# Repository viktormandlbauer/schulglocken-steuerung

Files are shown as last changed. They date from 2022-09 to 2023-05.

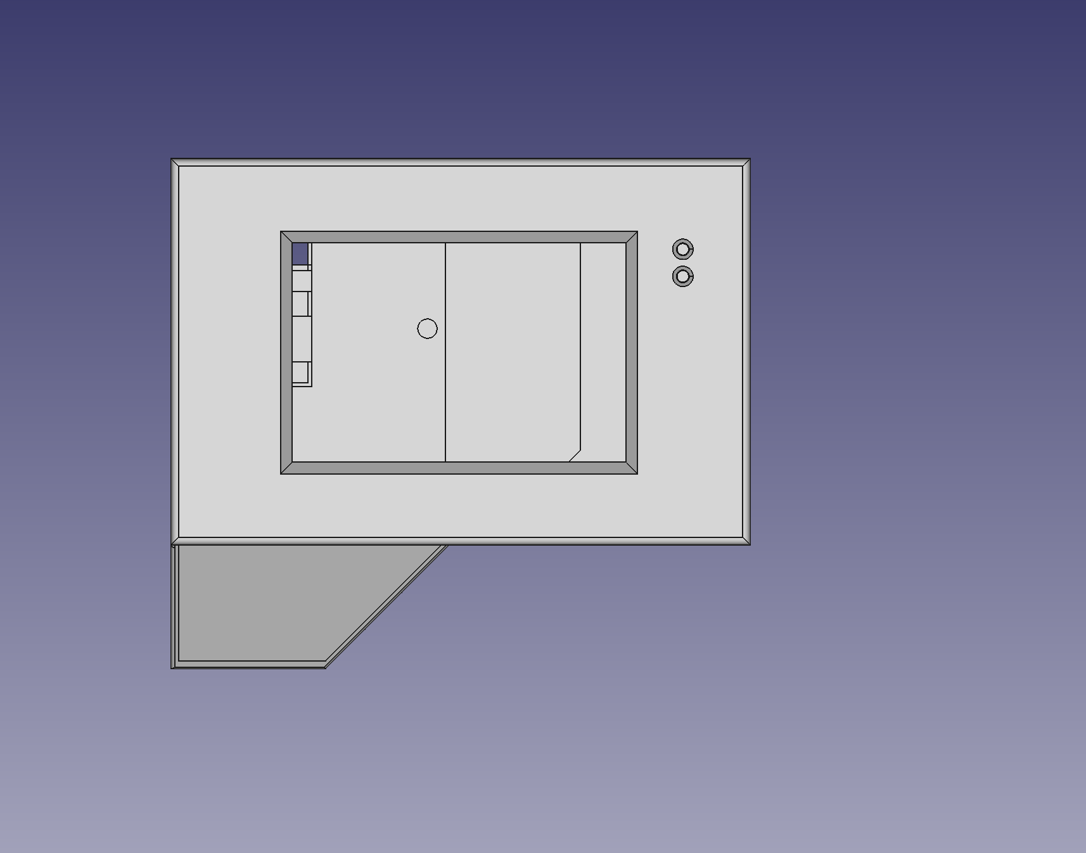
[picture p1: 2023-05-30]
cad/Freecad/CASE/A1_IMG/DiplPRJ3.png

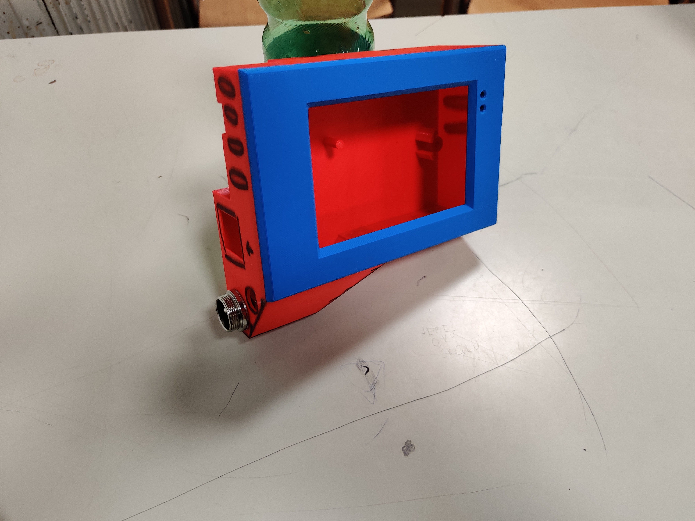
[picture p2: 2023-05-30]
cad/Freecad/CASE/A1_IMG/IMG_20230503_201758.jpg

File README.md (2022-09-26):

# schulglocken-steuerung
Google Drive Project:    
https://drive.google.com/drive/folders/1yu67mSQ9u2VfD9QC0o6wKGEjTrWiLxPo?usp=sharing

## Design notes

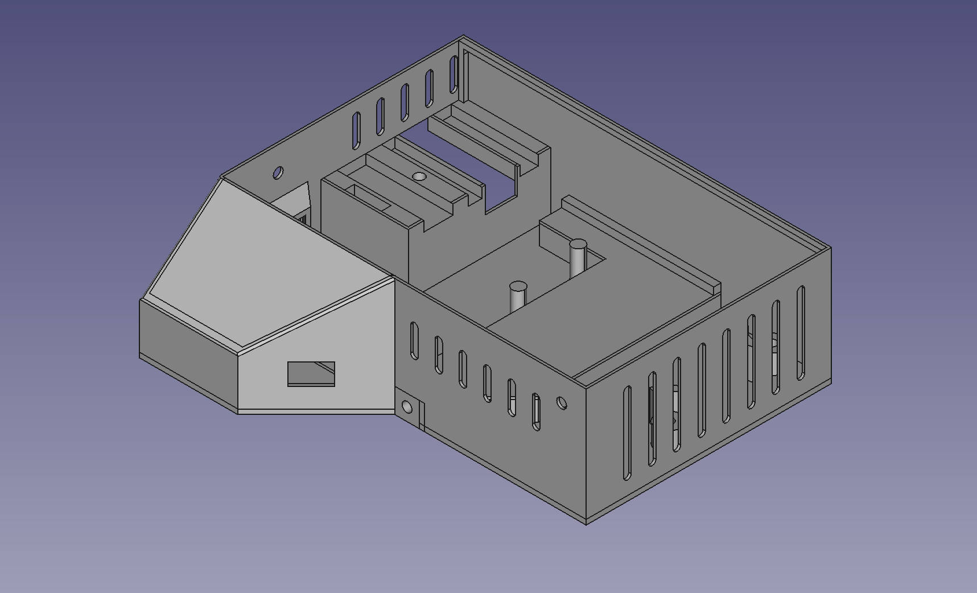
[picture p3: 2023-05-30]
cad/Freecad/CASE/A1_IMG/DiplPRJ4.png

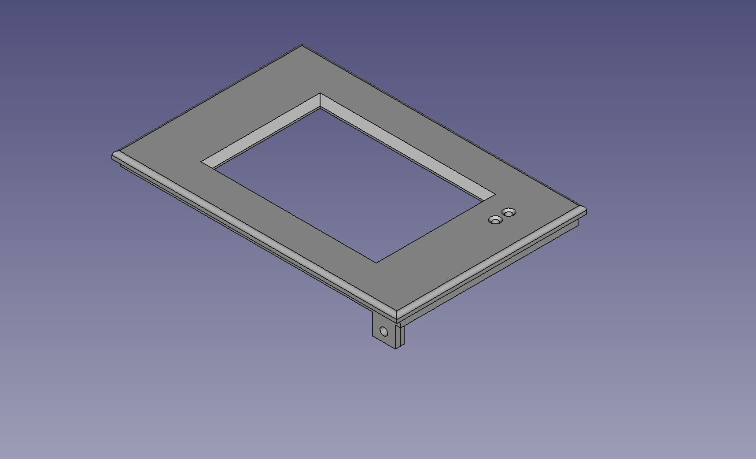
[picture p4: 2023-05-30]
cad/Freecad/CASE/A1_IMG/DiplPRJ5.png

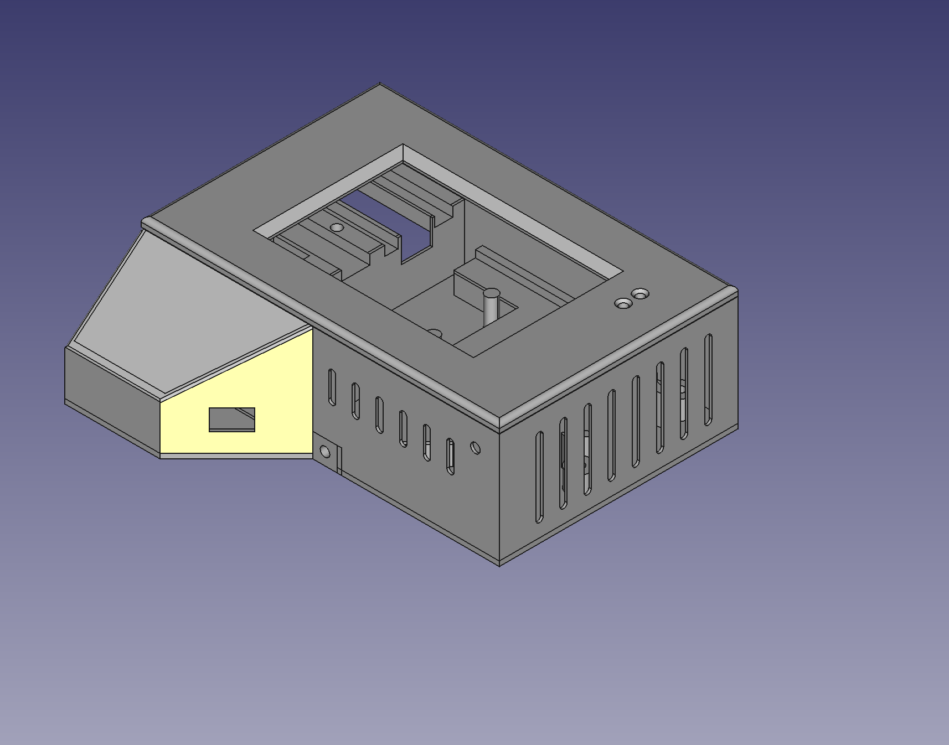
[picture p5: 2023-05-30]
cad/Freecad/CASE/A1_IMG/DiplPRJ2.png

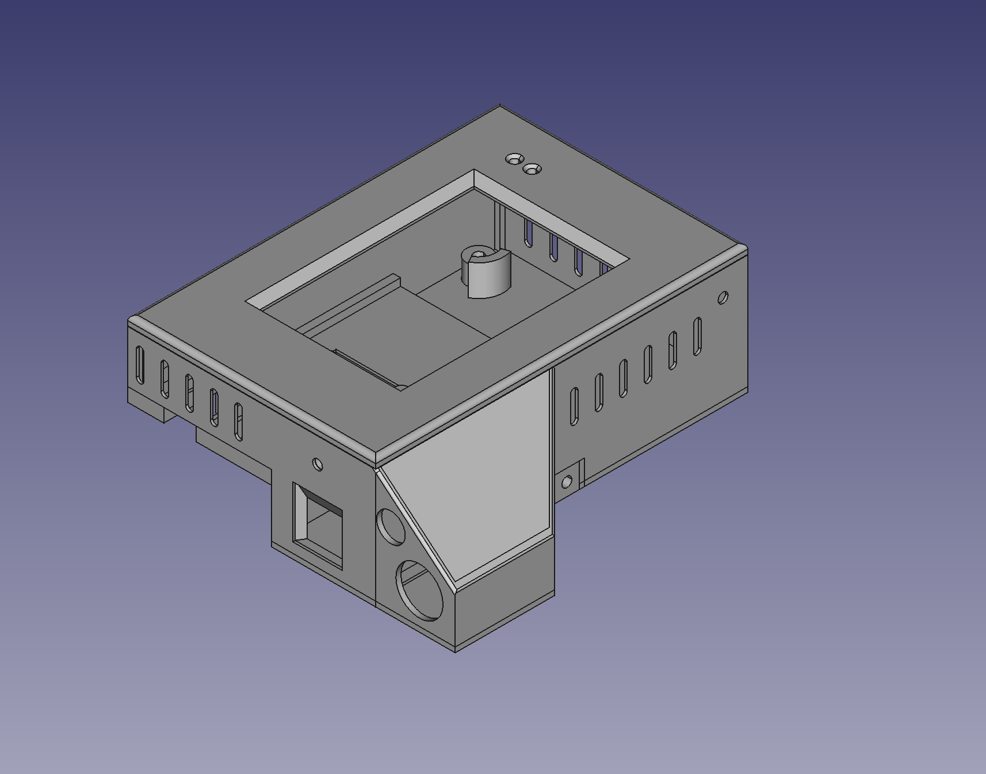
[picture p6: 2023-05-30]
cad/Freecad/CASE/A1_IMG/DiplPRJ1.png

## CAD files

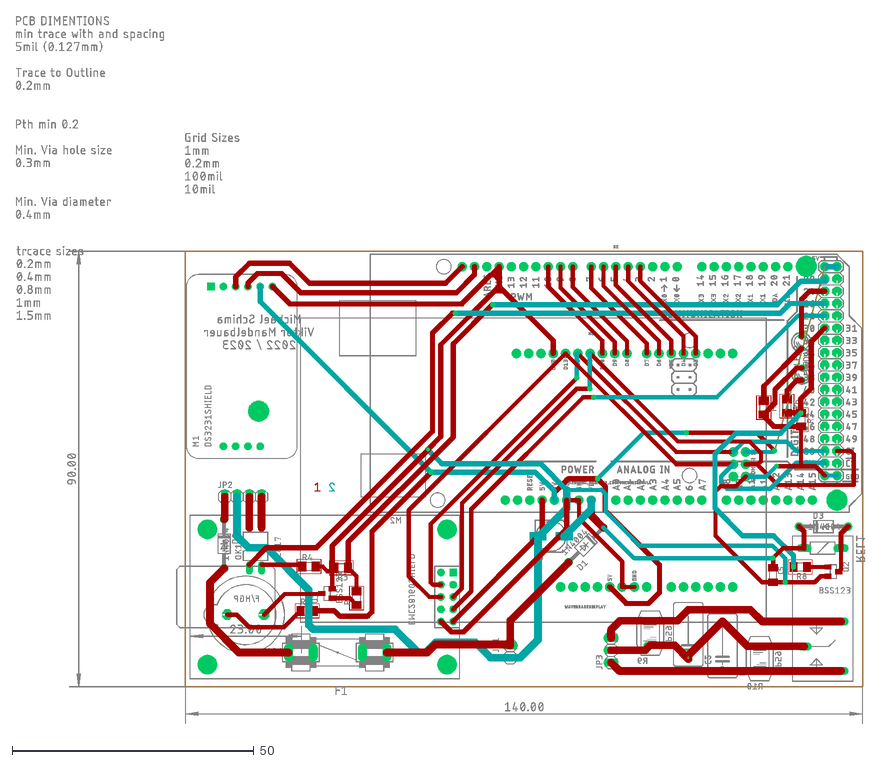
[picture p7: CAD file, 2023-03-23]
cad/Eagle/Eagle MainPCB/Schulglocke_PCB.dxf
175.5 x 146.2

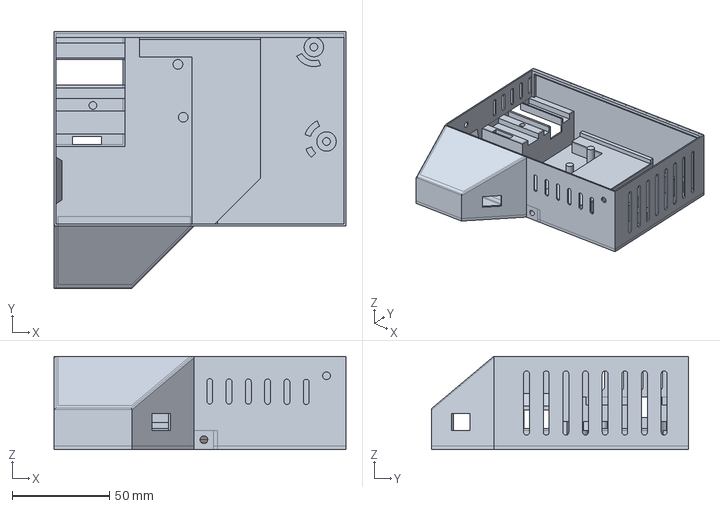
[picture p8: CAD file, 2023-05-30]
cad/Freecad/CASE/leftcorner_v5.FCStd
150.0 x 132.0 x 48.0 mm
base body witch cut out001
WallBracket

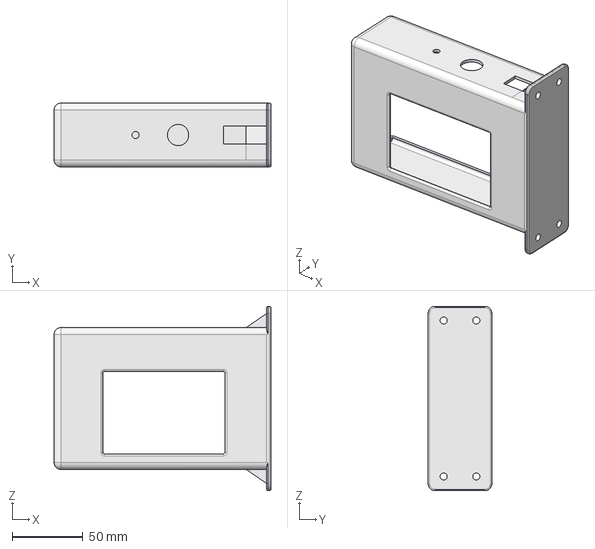
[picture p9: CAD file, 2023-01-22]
cad/Freecad/DEMO1/demo1_cut.FCStd
153.0 x 45.0 x 130.0 mm

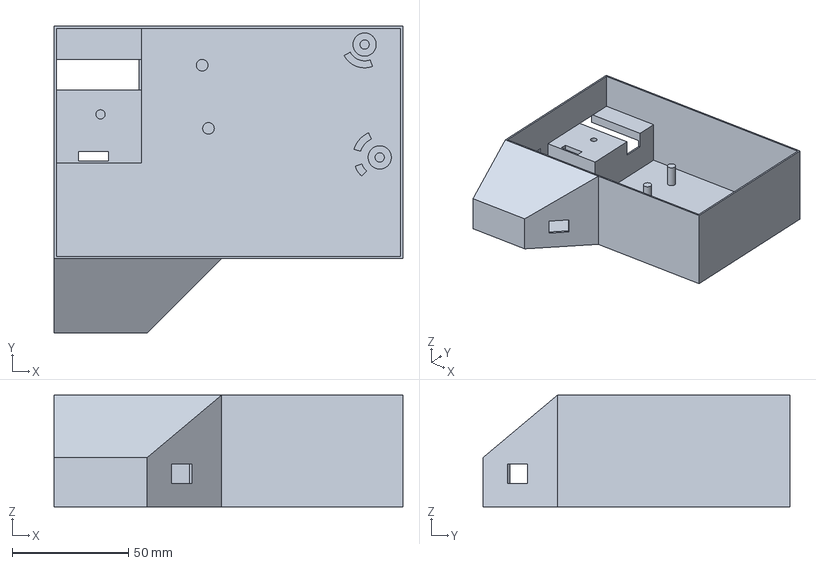
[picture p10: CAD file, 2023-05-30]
cad/Freecad/CASE/leftcorner-base body witch cut out001.3mf
150.0 x 132.0 x 48.0 mm

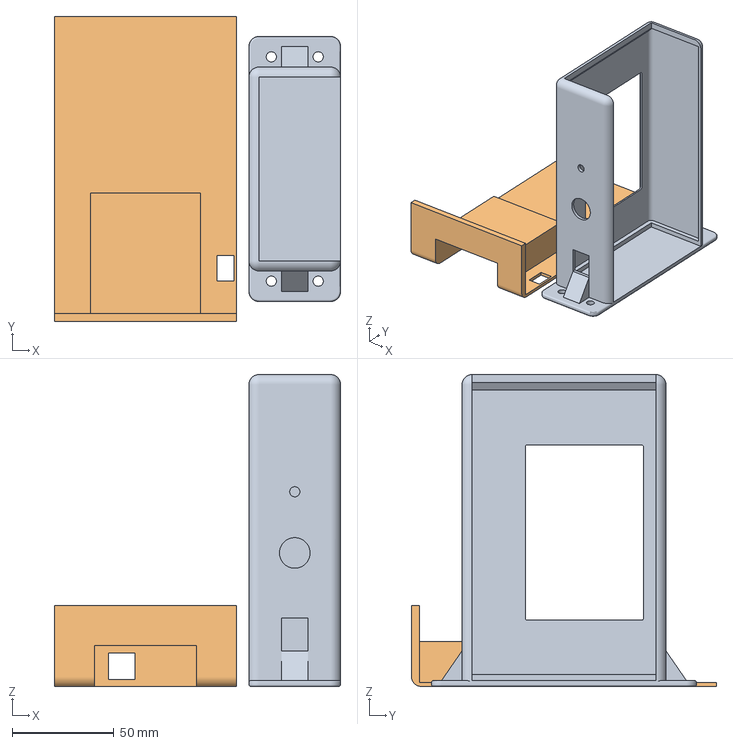
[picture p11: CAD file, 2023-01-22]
cad/Freecad/DEMO1/demo1_cut-Body006.3mf
140.4 x 149.7 x 153.0 mm
demo1_cut-Body006

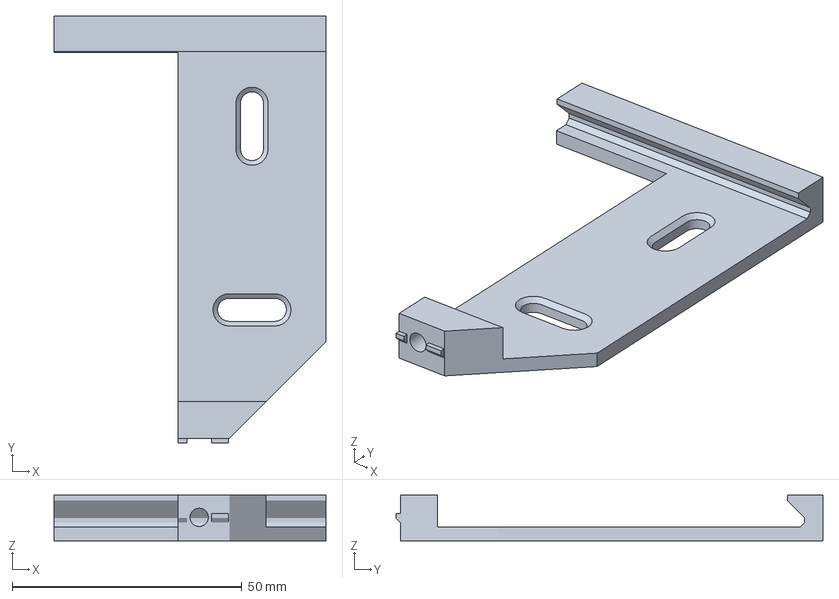
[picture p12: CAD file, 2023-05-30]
cad/Freecad/CASE/leftcorner_v5-WallBracket.3mf
59.2 x 93.0 x 10.0 mm

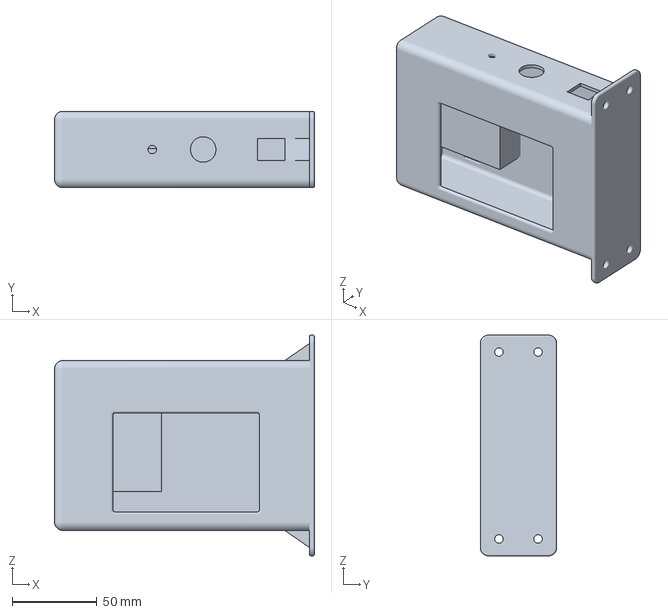
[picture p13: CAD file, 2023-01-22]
cad/Freecad/DEMO1/demo1-Body.3mf
153.0 x 45.0 x 130.0 mm

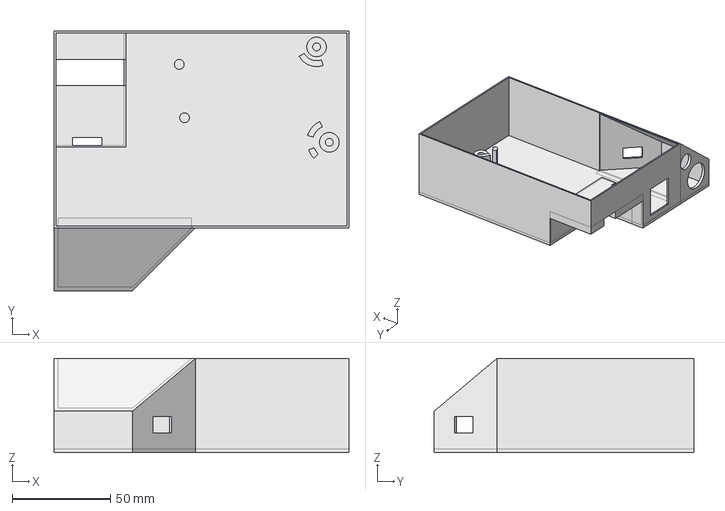
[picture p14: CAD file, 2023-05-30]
cad/Freecad/CASE/leftcorner.FCStd
150.0 x 132.0 x 48.0 mm

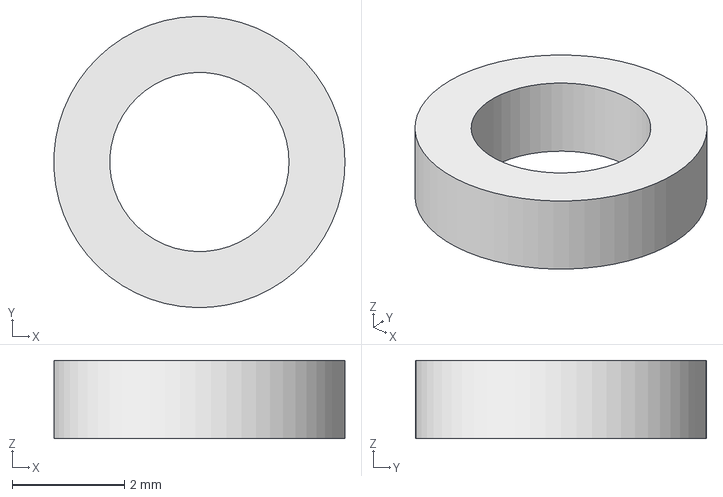
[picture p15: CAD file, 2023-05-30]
cad/Freecad/CASE/isolation.FCStd
5.20 x 5.20 x 1.40 mm

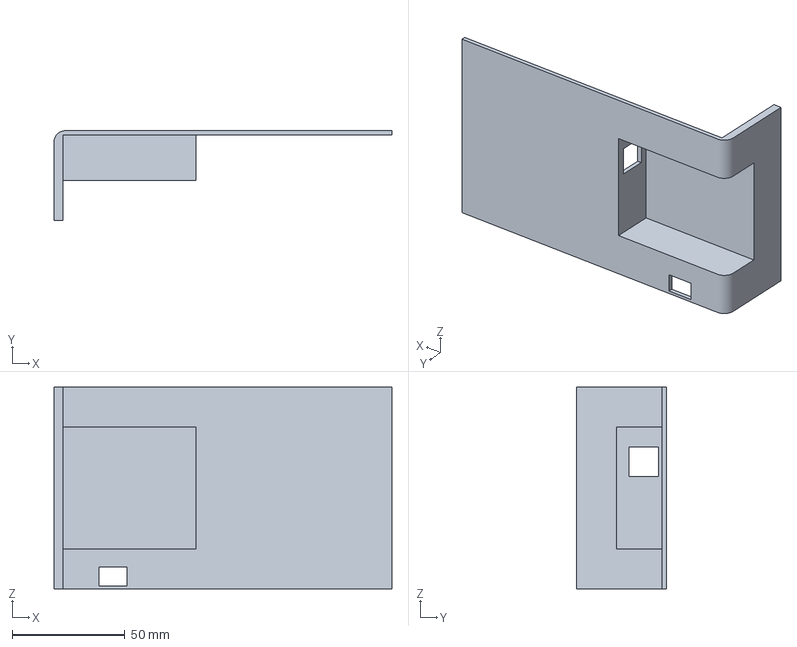
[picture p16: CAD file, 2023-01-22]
cad/Freecad/DEMO1/part2.3mf
149.7 x 39.7 x 89.4 mm

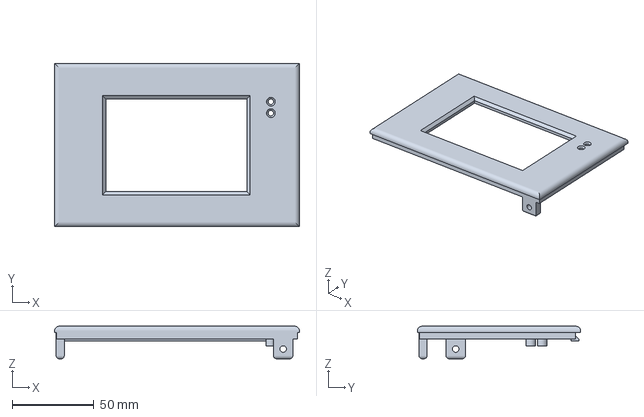
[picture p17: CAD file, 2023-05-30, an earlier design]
cad/Freecad/CASE/leftcorner_v4-Body008.3mf
150.0 x 100.0 x 20.0 mm

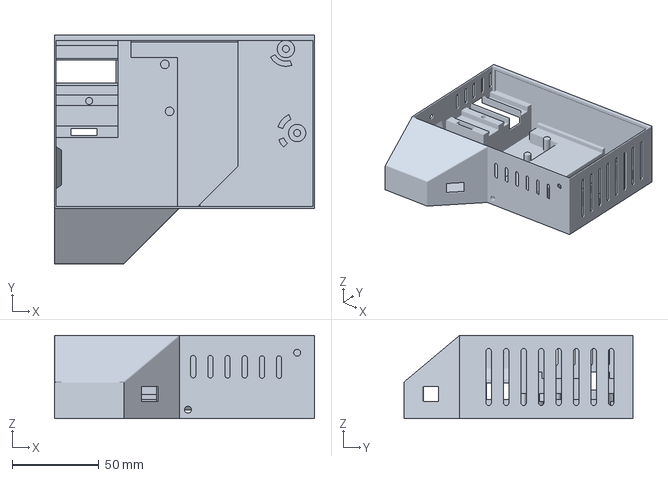
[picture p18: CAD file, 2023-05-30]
cad/Freecad/CASE/leftcorner_v4-base body witch cut out001.3mf
150.0 x 132.0 x 48.0 mm

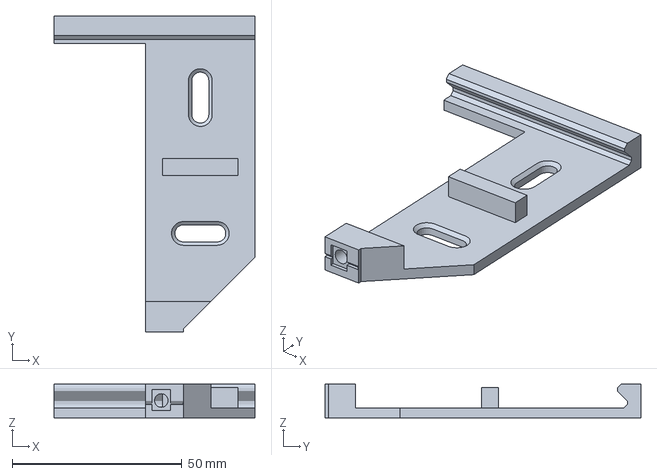
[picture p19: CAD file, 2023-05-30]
cad/Freecad/CASE/leftcorner_v5-WallBracketPad041.3mf
59.2 x 93.0 x 10.0 mm

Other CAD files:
cad/Freecad/DEMO1/demo1.FCStd
cad/Freecad/DEMO1/part1.3mf
cad/Freecad/CASE/leftcorner-MOUNT_v3-Body.3mf
cad/Freecad/CASE/isolation-Body.3mf
cad/Freecad/CASE/1.FCStd
cad/Freecad/CASE/1-Body007.3mf
cad/Freecad/CASE/1-base body witch cut out001.3mf
cad/Freecad/CASE/1_long edge.FCStd
cad/Freecad/CASE/leftcorner_v2.FCStd
cad/Freecad/CASE/leftcorner_v3-base body witch cut out001.3mf
cad/Freecad/CASE/leftcorner_v3.FCStd
cad/Freecad/CASE/leftcorner_v4.FCStd

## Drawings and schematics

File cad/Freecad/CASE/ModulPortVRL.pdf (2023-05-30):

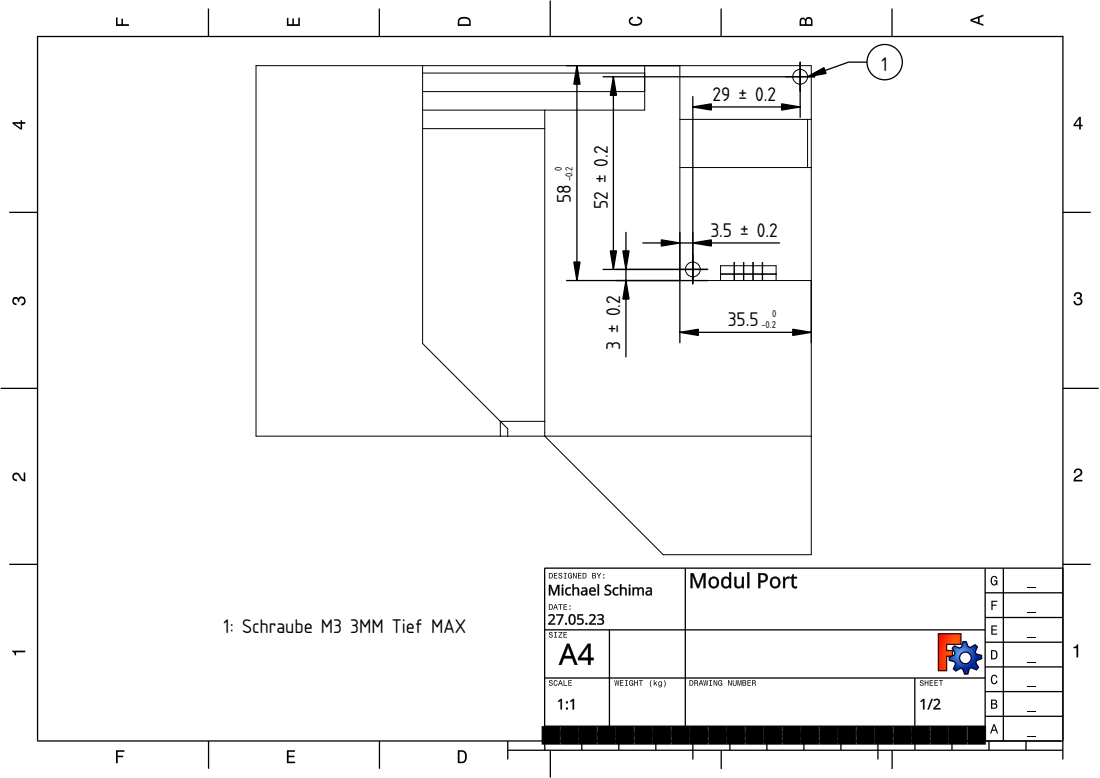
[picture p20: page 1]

1: Schraube M3 3MM Tief MAX

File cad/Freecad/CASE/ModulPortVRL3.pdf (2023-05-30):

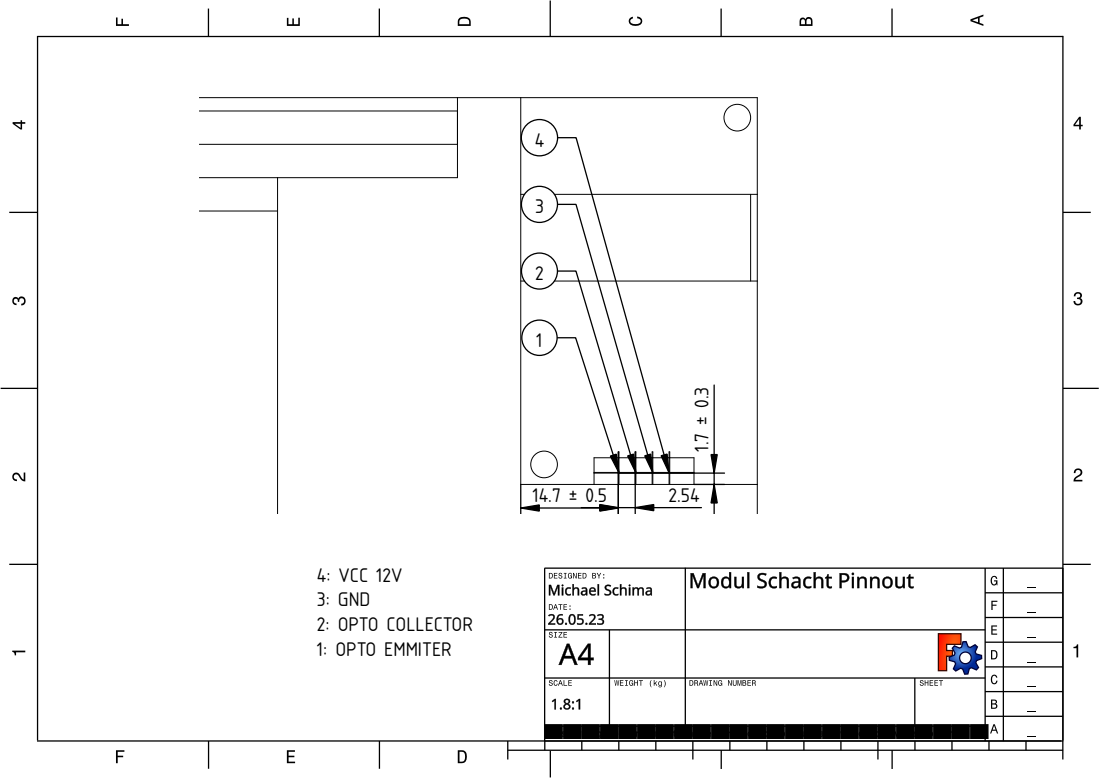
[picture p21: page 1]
4: VCC 12V 3: GND 2: OPTO COLLECTOR 1: OPTO EMMITER

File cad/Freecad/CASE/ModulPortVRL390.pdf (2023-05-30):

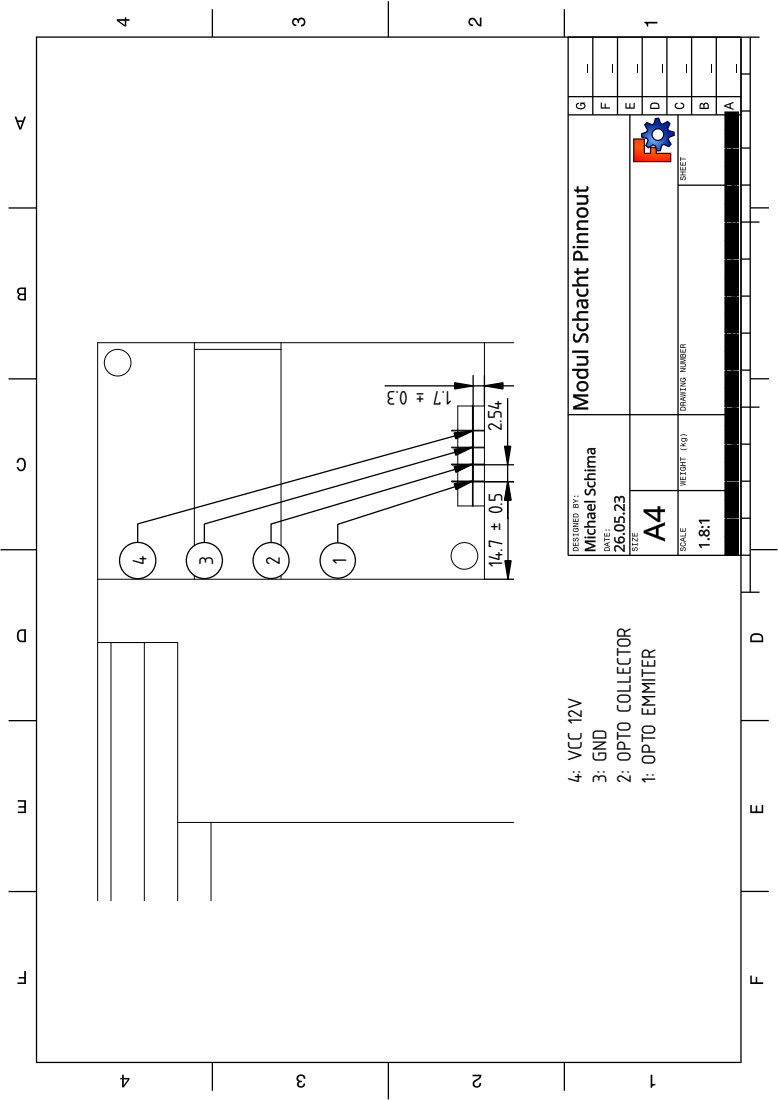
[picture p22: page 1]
4: VCC 12V; 3: GND; 2: OPTO COLLECTOR 1: OPTO EMMITER

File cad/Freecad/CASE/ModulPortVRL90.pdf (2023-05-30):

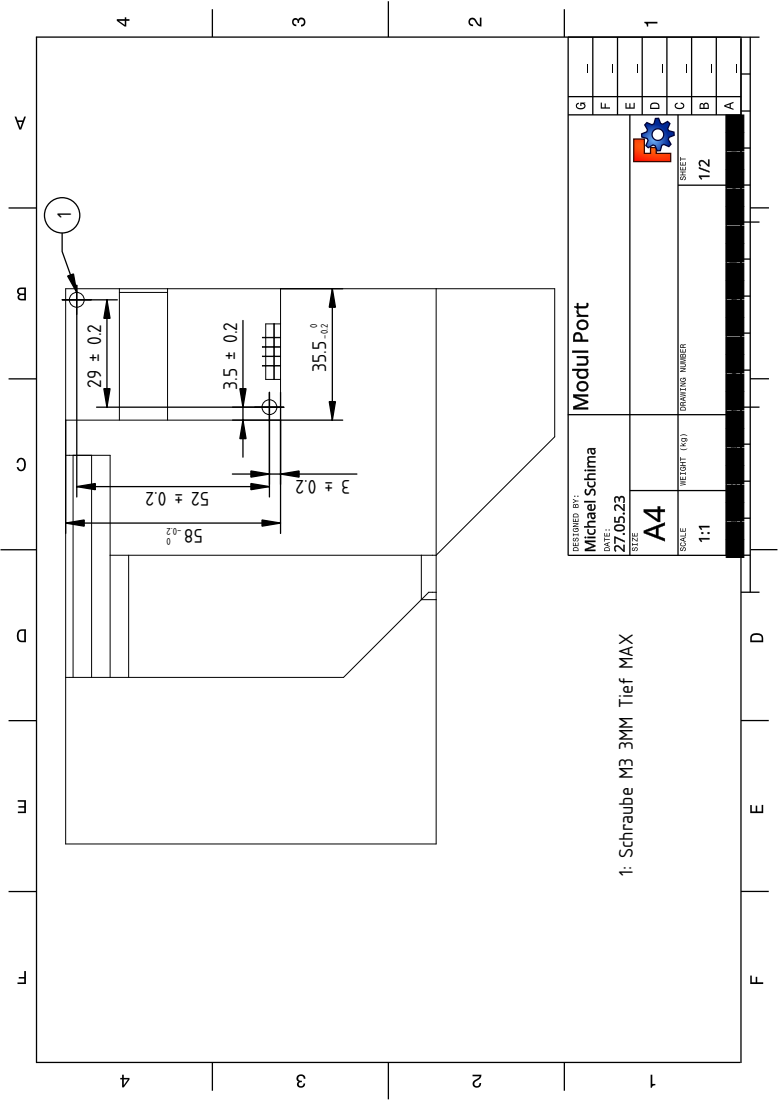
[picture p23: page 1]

1: Schraube M3 3MM Tief MAX

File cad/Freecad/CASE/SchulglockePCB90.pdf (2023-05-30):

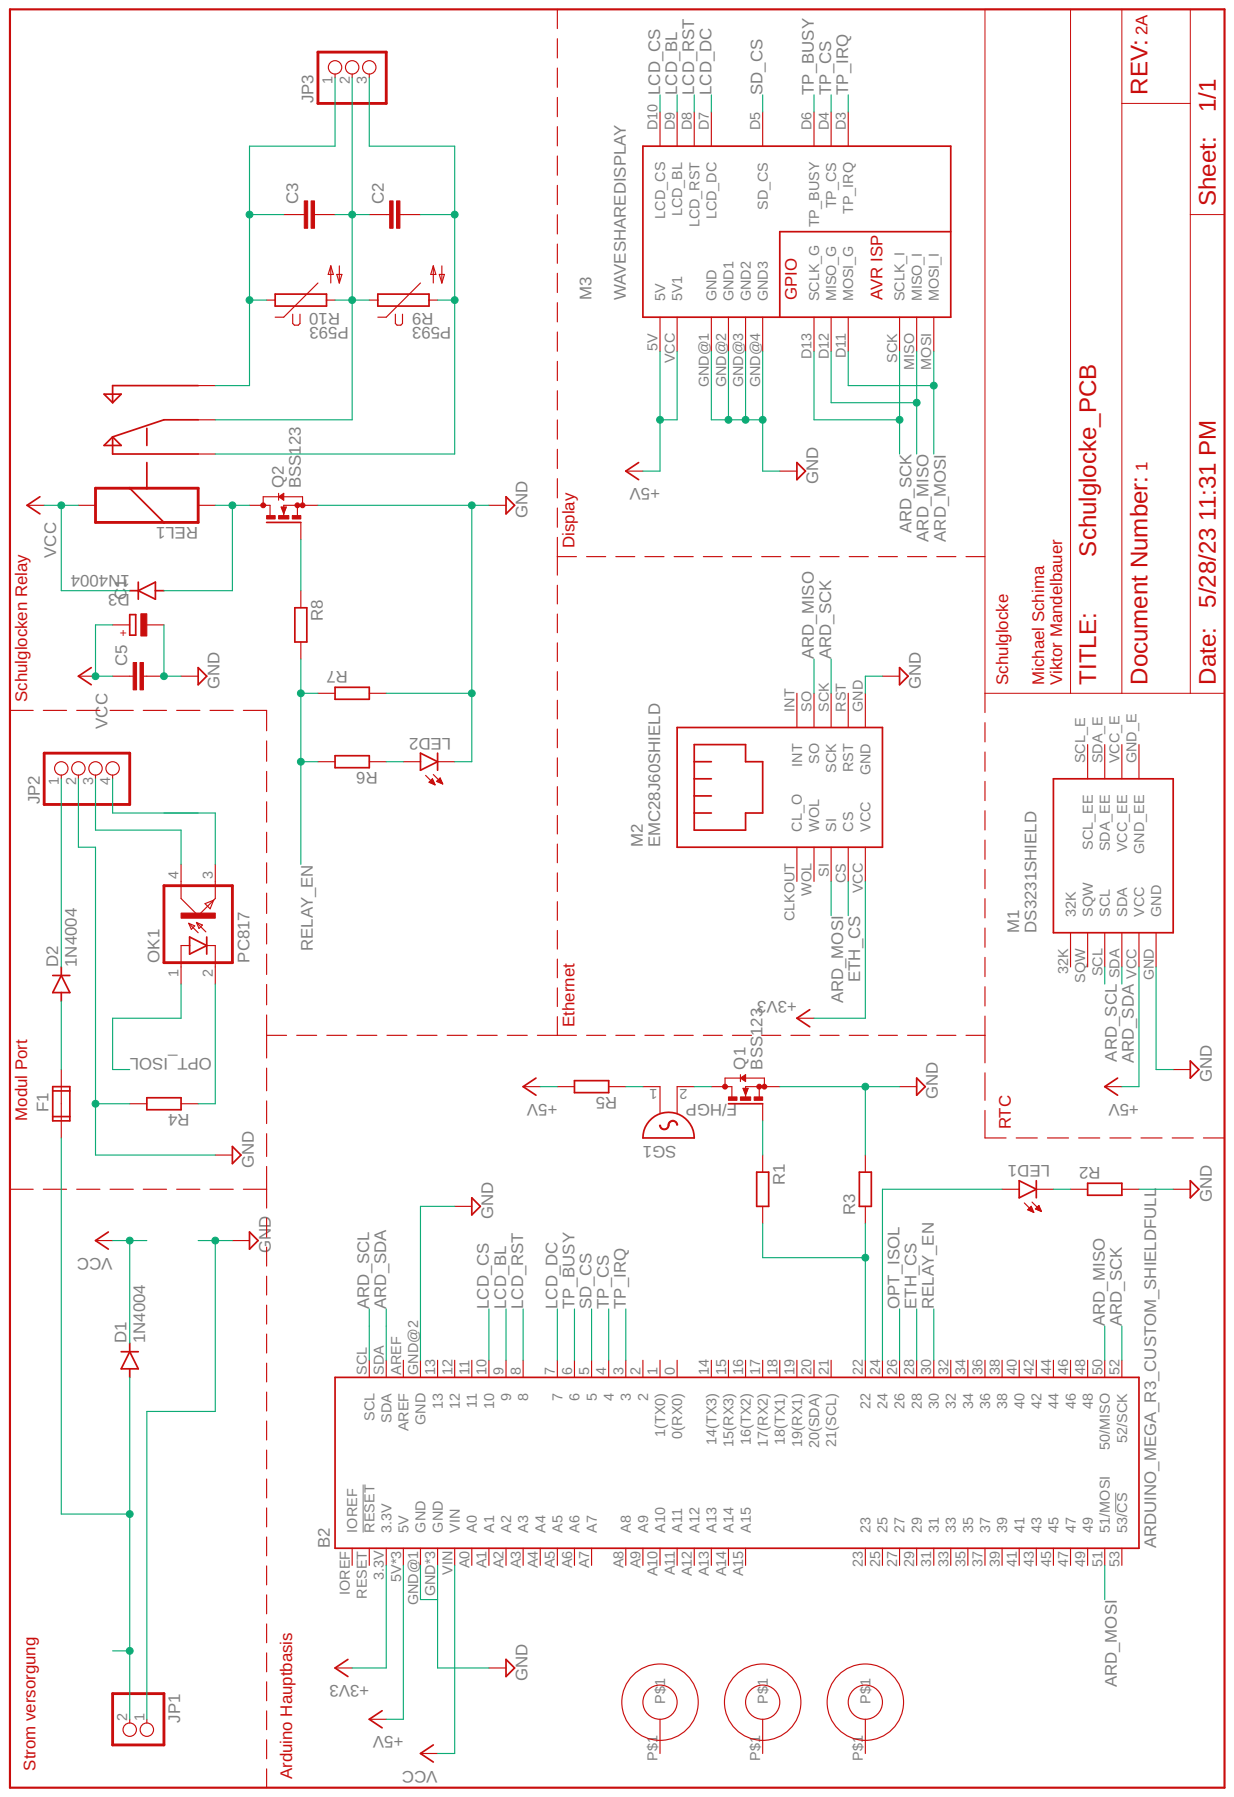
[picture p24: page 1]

Schulglocke Michael Schima Viktor Mandelbauer 1 2A

5V1 VCC GND1 GND@2 GND2 GND@3 GND3 GND@4

SCK RST RST GND GND

CLKOUT WOL WOL SI SI CS CS

Strom versorgung Modul Port

GND GND@2 GND GND@1 SDA

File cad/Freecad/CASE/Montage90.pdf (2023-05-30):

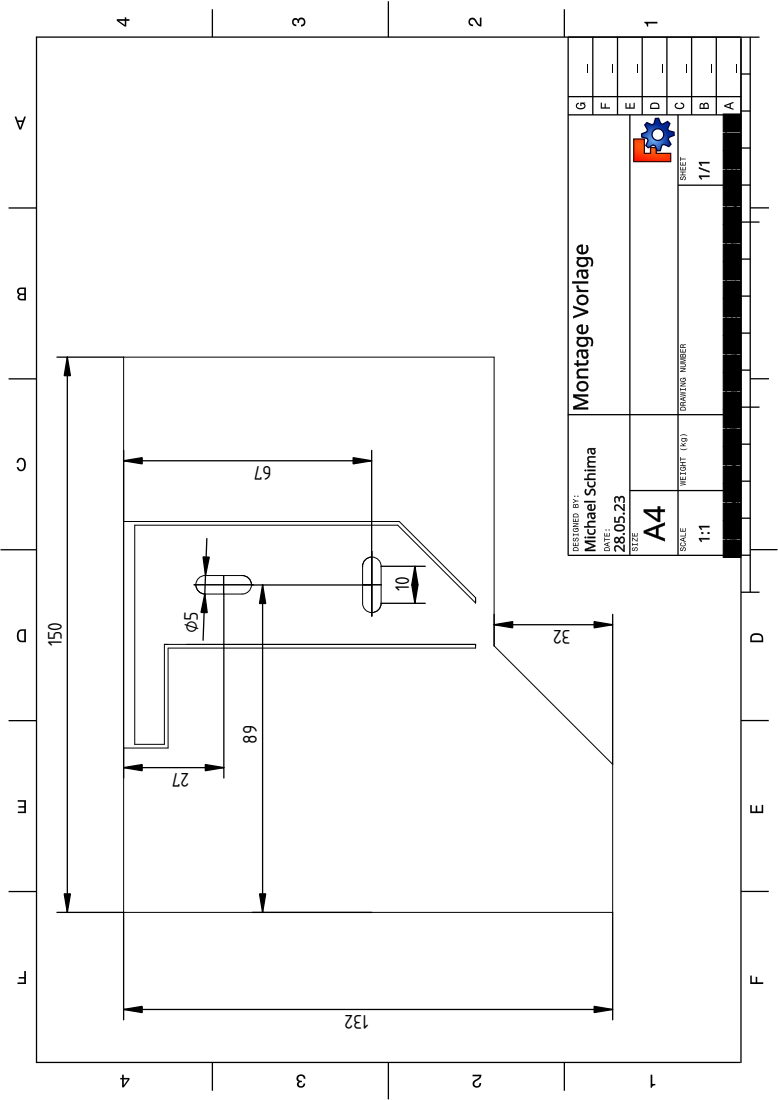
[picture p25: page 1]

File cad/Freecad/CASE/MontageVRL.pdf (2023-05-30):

150

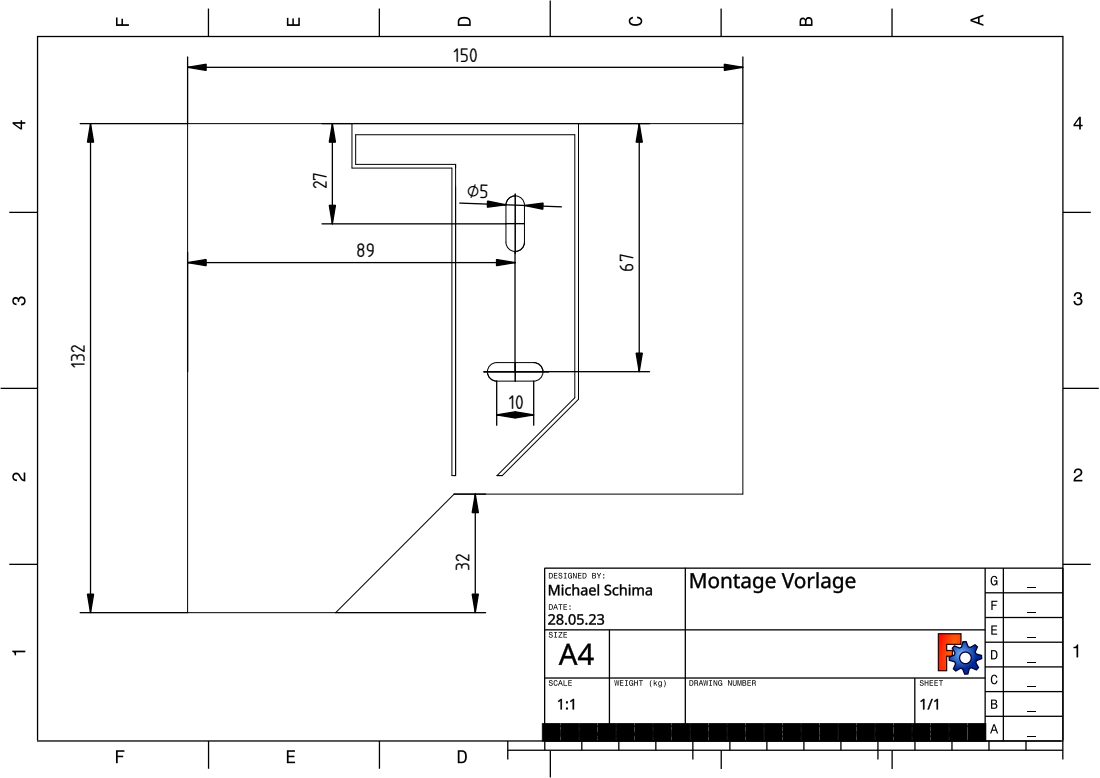
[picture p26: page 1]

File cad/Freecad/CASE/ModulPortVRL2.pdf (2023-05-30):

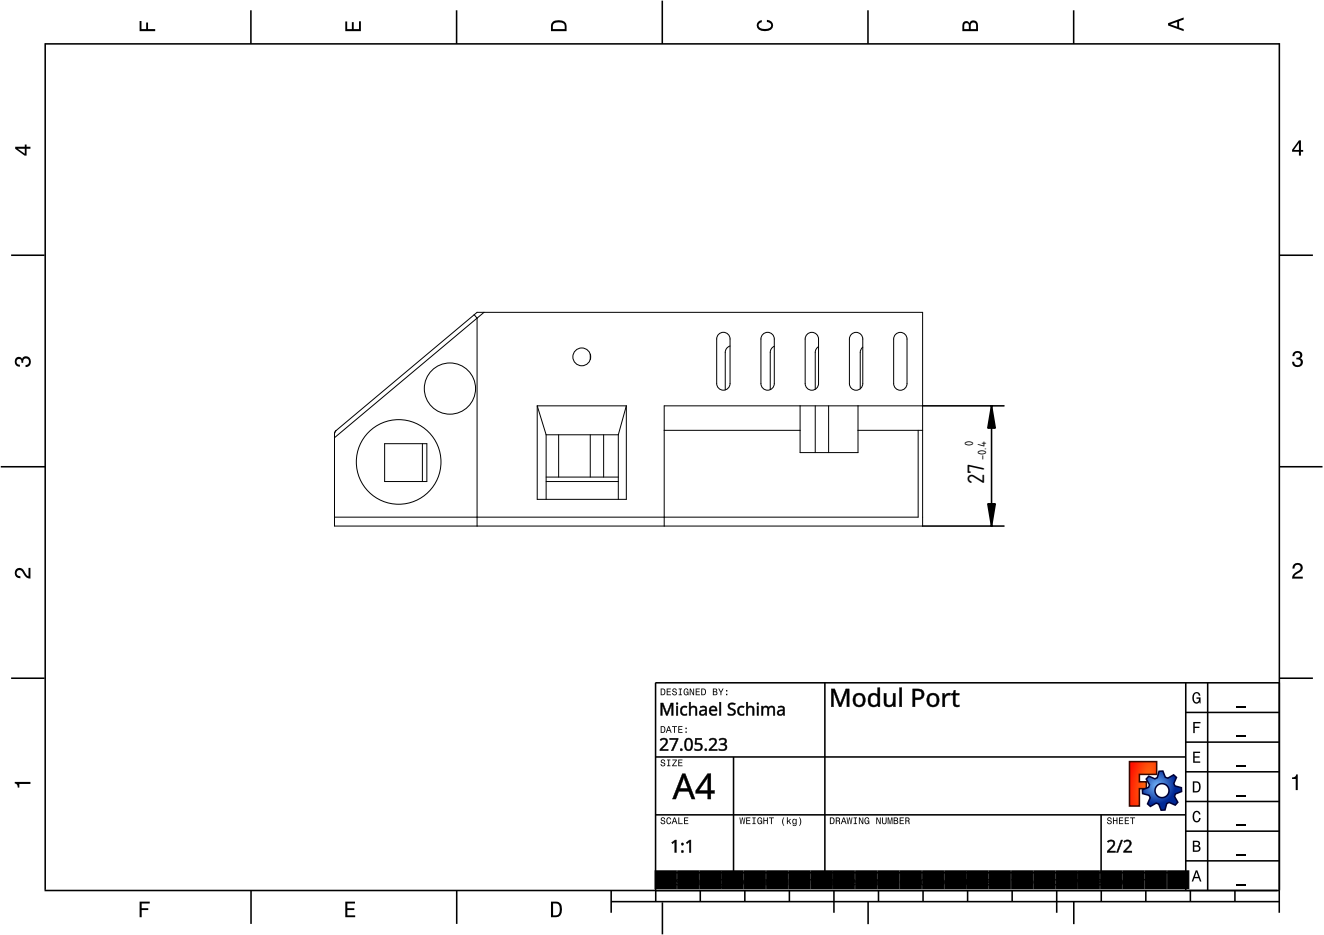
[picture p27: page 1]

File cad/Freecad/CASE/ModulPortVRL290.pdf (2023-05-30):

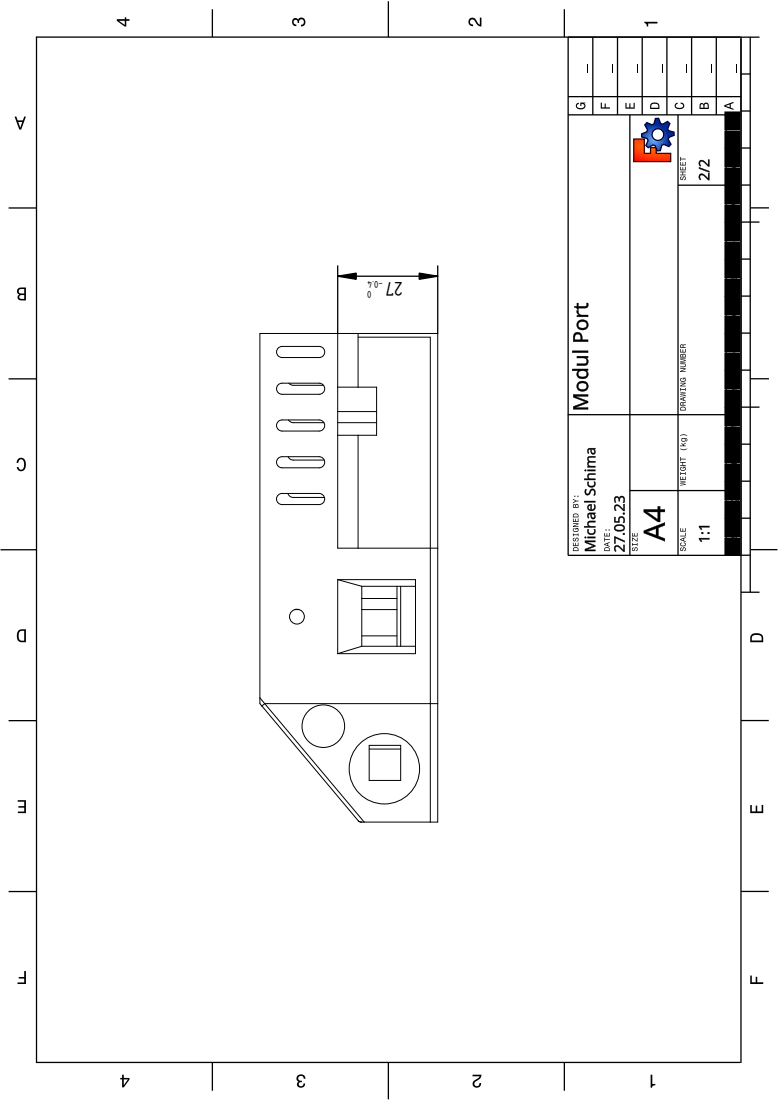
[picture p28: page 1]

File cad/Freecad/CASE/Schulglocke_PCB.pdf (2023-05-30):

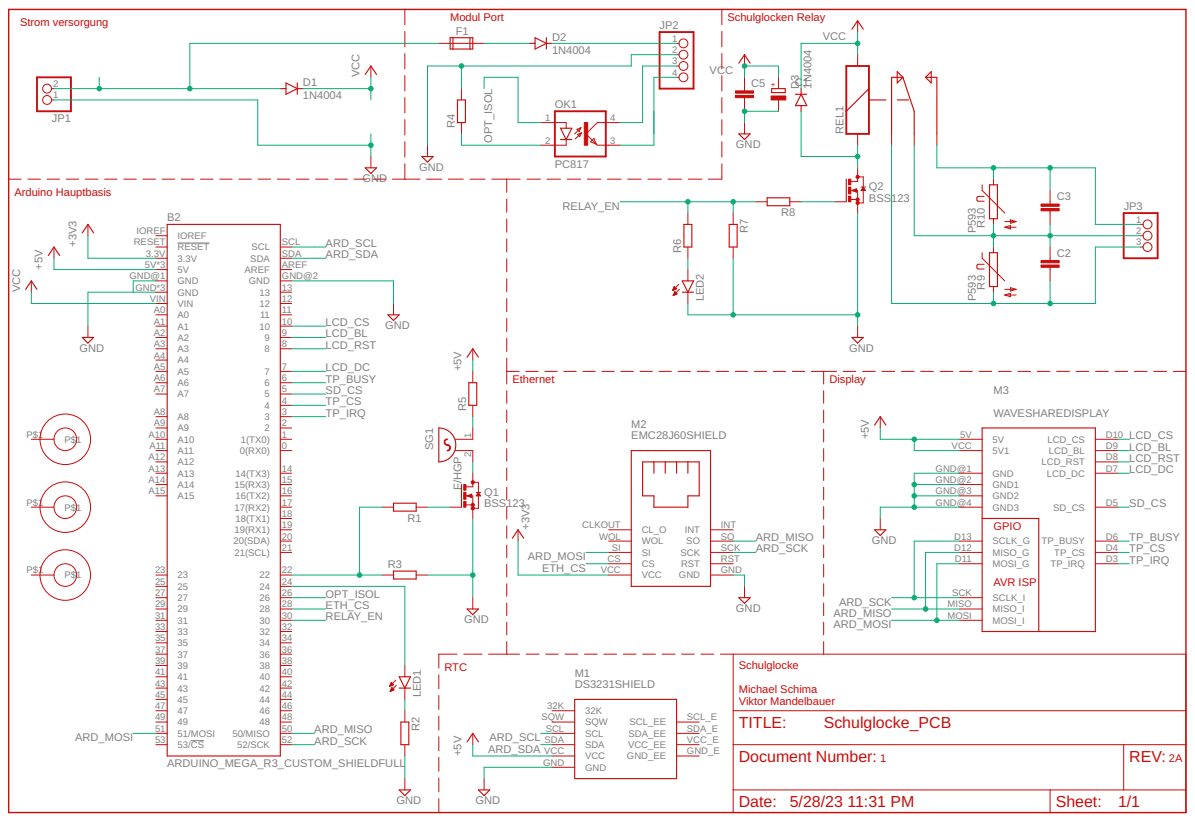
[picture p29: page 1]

Document Number: | REV:

Date: 5/28/23 11:31 PM | Sheet: 1/1

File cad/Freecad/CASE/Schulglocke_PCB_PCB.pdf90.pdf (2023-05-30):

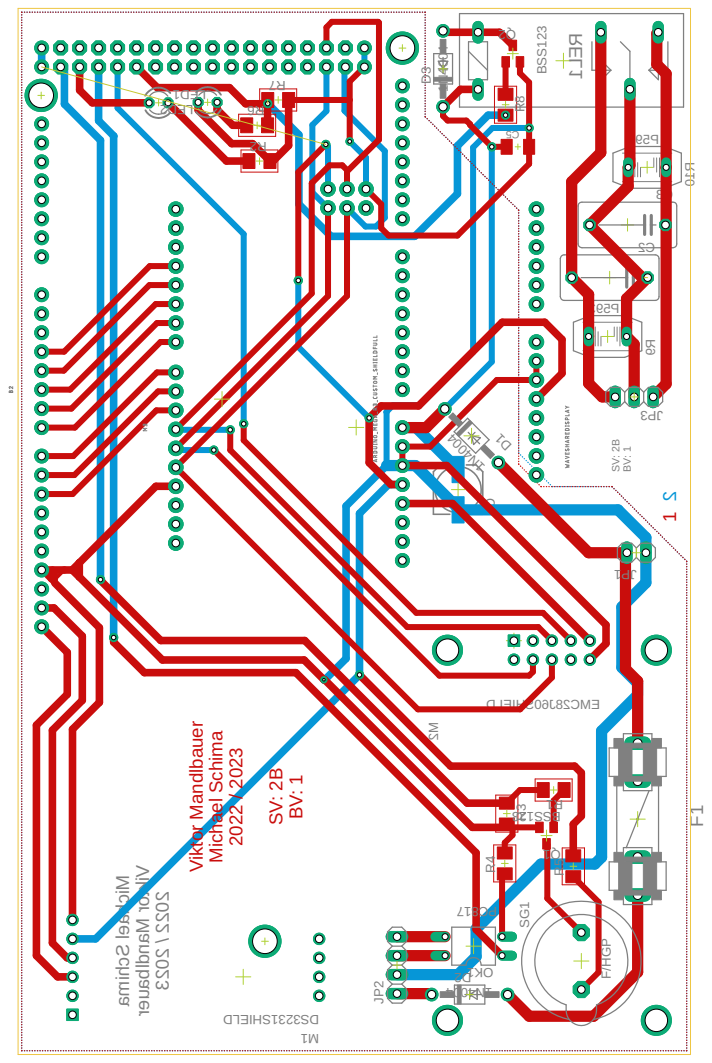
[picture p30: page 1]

DLEI HS06J82 CME 395P 395P Michael Schima Viktor Mandlbauer 2022 / 2023 2 C3 C M2 R10 R9 C1 REL1 2 1 Viktor Mandlbauer Michael Schima 2022 / 2023 SV: 2B BV: 1 SV: 2B BV: 1D1 2 D D3 1PJ JP2 3PJ 1 DEL 2 DEL 1 Q 2 Q 1 R 2 R R3 R4 R5 6 R 7 R R8 SG1 1KO F1 5 C 1 M 1N40 4 4004 N1 1N4004 321SSB BSS123 F/HGP 718 CP DLEI HS1323SD

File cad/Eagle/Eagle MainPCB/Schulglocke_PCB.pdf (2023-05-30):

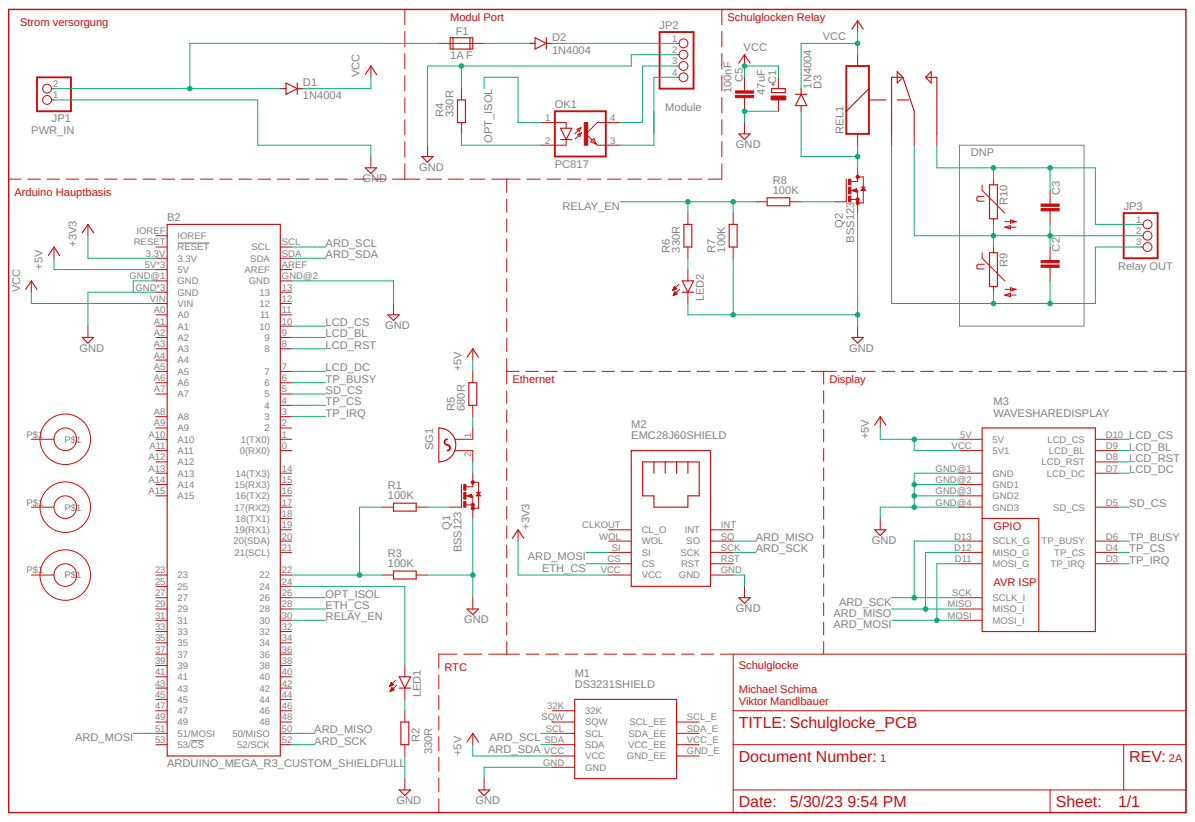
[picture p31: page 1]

Document Number: | REV:

Date: 5/30/23 9:54 PM | Sheet: 1/1

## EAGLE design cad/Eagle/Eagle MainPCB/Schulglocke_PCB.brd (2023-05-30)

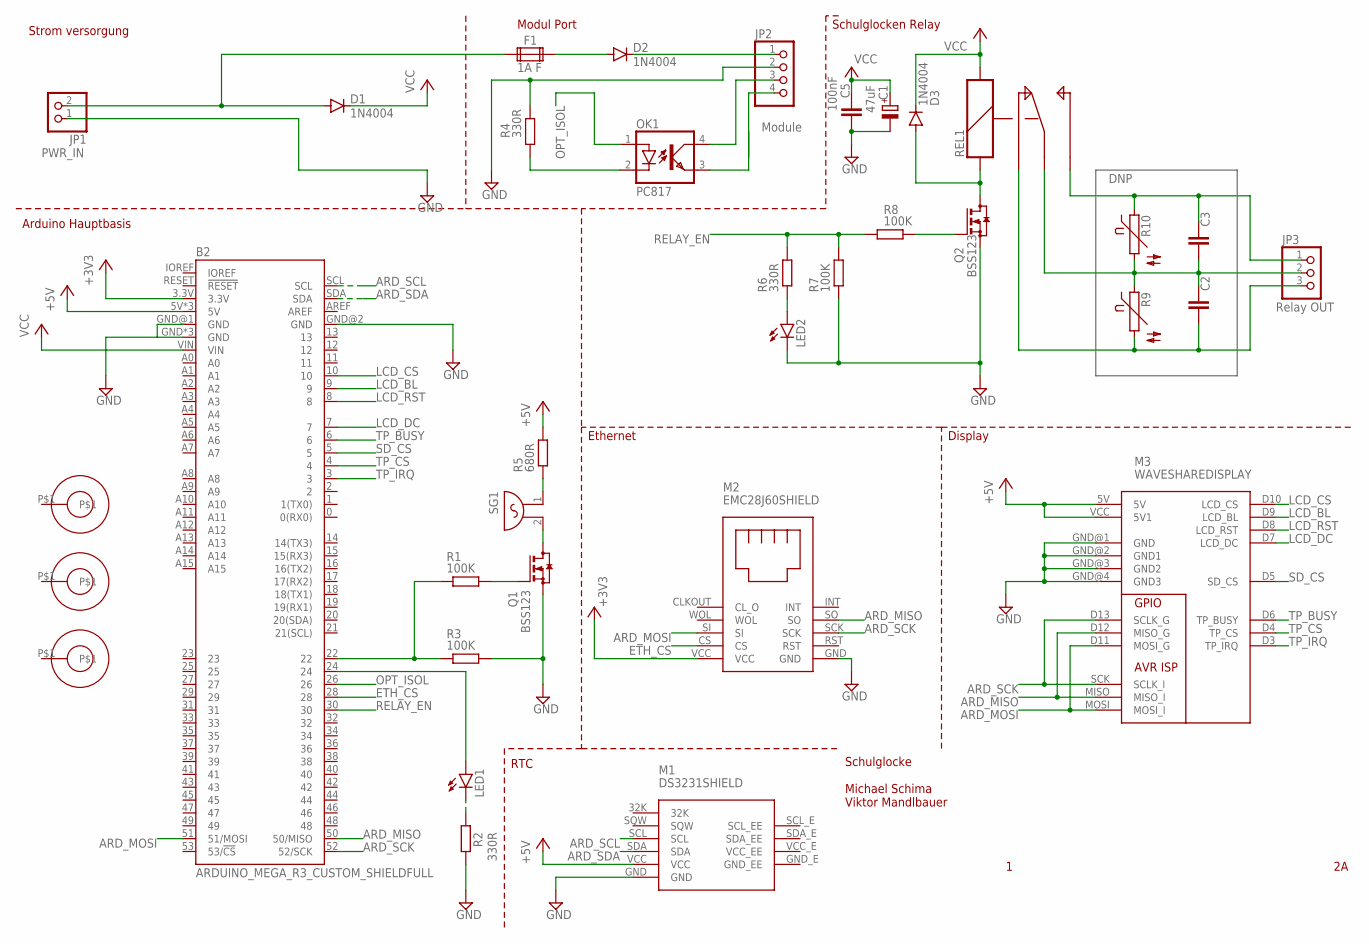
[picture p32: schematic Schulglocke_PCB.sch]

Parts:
B2: ARDUINO_MEGA_R3_CUSTOM_SHIELDFULL; ARDUINO_MEGA_NO_SILK
C1: 47uF; 153CLV-0605
C2, C3: DNP; C102-064X133
C5: 100nF; C1206K
D1, D2, D3: 1N4004; DO41-10
F1: 1A F; FUSE1
JP1: PINHD-1X2; 1X02
JP2: PINHD-1X4; 1X04
JP3: PINHD-1X3; 1X03
LED1, LED2: LED3MM
M1: DS3231SHIELD; DS3231_F
M2: EMC28J60SHIELD; EMC_F
M3: WAVESHAREDISPLAY; ARDUINO_R3_NO_HOLES
OK1: PC817; DIL04
Q1, Q2: BSS123; SOT23
R1, R3, R7, R8: 100K; M1206
R2, R4, R6: 330R; M1206
R5: 680R; M1206
R9, R10: P593
REL1: REL-5PIN
SG1: F/HGP
U$1, U$2, U$3: MOUNTPOINT3.3MM; MOUNT_POINT_3.3MM

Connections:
+3V3: B2.3.3V, M2.VCC
+5V: B2.5V, B2.5V@1 (5V), B2.5V@2 (5V), M1.VCC, M3.5V, M3.VCC (5V1), R5.2
ARD_MISO: B2.50 (50/MISO), M2.SO, M3.D12 (MISO_G), M3.MISO (MISO_I)
ARD_MOSI: B2.51 (51/MOSI), M2.SI, M3.D11 (MOSI_G), M3.MOSI (MOSI_I)
ARD_SCK: B2.52 (52/SCK), M2.SCK, M3.D13 (SCLK_G), M3.SCK (SCLK_I)
ARD_SCL: B2.SCL, M1.SCL
ARD_SDA: B2.SDA, M1.SDA
ETH_CS: B2.28, M2.CS
GND: B2.GND, B2.GND@1 (GND), B2.GND@2 (GND), B2.GND@3 (GND), B2.GND@4 (GND), C1.-, C5.2, JP1.1, JP2.2, LED2.K (C), M1.GND, M2.GND, M3.GND@1 (GND), M3.GND@2 (GND1), M3.GND@3 (GND2), M3.GND@4 (GND3), Q1.2 (S), Q2.2 (S), R2.2, R3.2, R4.2, R7.2
LCD_BL: B2.9, M3.D9 (LCD_BL)
LCD_CS: B2.10, M3.D10 (LCD_CS)
LCD_DC: B2.7, M3.D7 (LCD_DC)
LCD_RST: B2.8, M3.D8 (LCD_RST)
unnamed: C2.1, C3.2, JP3.2, R9.1, R10.2, REL1.C
unnamed: C3.1, JP3.1, R10.1, REL1.O
unnamed: C2.2, JP3.3, R9.2, REL1.S
unnamed: D2.A, F1.2A
unnamed: D2.C, JP2.1
unnamed: JP2.3, OK1.4 (COL)
unnamed: JP2.4, OK1.3 (EMIT)
unnamed: D1.A, F1.1A, JP1.2
unnamed: D3.A, Q2.3 (D), REL1.S1
unnamed: B2.24, LED1.A
unnamed: LED2.A, R6.1
unnamed: R5.1, SG1.1
unnamed: Q1.3 (D), SG1.2
unnamed: B2.22, R1.2, R3.1
unnamed: Q1.1 (G), R1.1
unnamed: OK1.2 (C), R4.1
unnamed: Q2.1 (G), R8.1
unnamed: LED1.K (C), R2.1
OPT_ISOL: B2.26, OK1.1 (A)
RELAY_EN: B2.30, R6.2, R7.1, R8.2
SD_CS: B2.5, M3.D5 (SD_CS)
TP_BUSY: B2.6, M3.D6 (TP_BUSY)
TP_CS: B2.4, M3.D4 (TP_CS)
TP_IRQ: B2.3, M3.D3 (TP_IRQ)
VCC: B2.VIN, C1.+, C5.1, D1.C, D3.C, REL1.S2

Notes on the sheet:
Schulglocke Michael Schima Viktor Mandlbauer
Arduino Hauptbasis
Strom versorgung
Modul Port
Display
Ethernet
RTC
Schulglocken Relay
DNP
PWR_IN
Module
Relay OUT

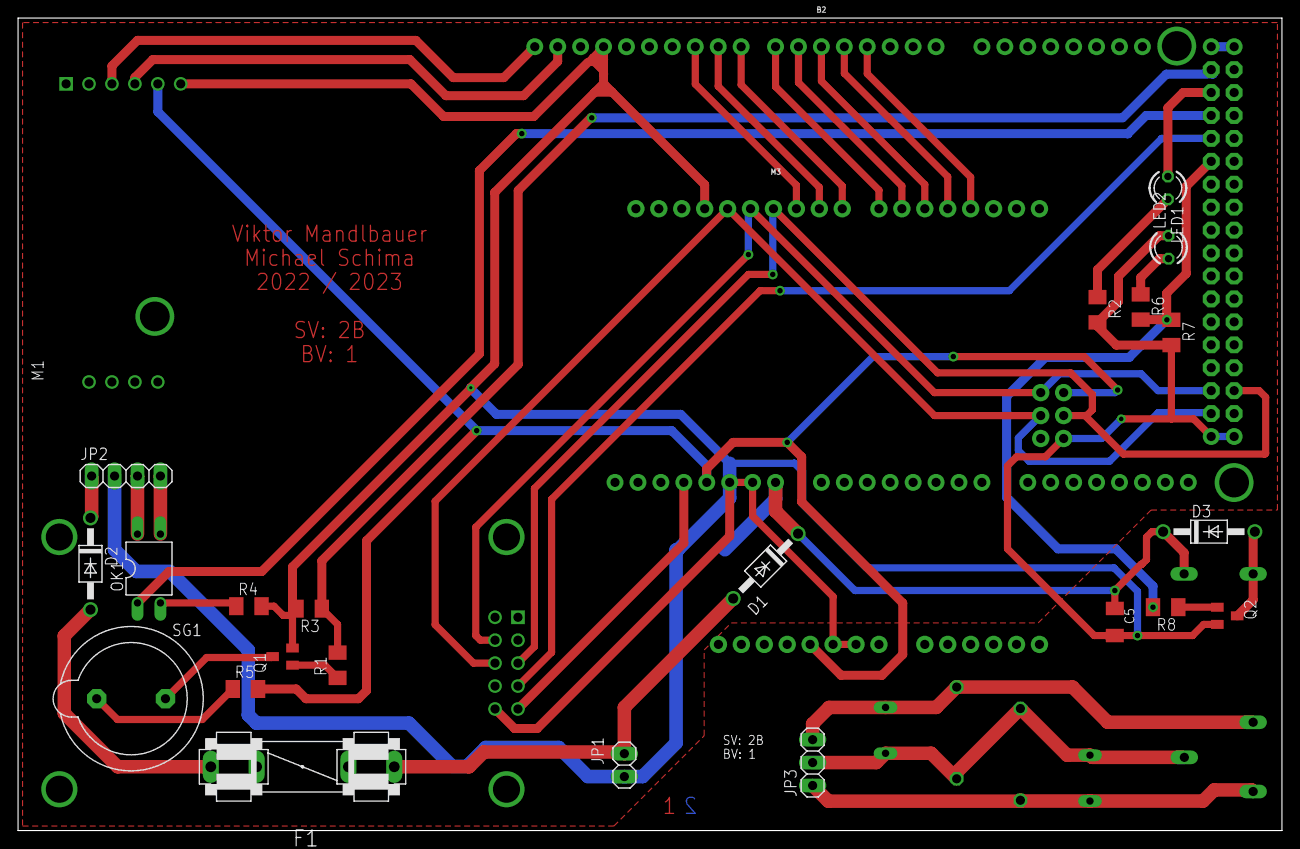
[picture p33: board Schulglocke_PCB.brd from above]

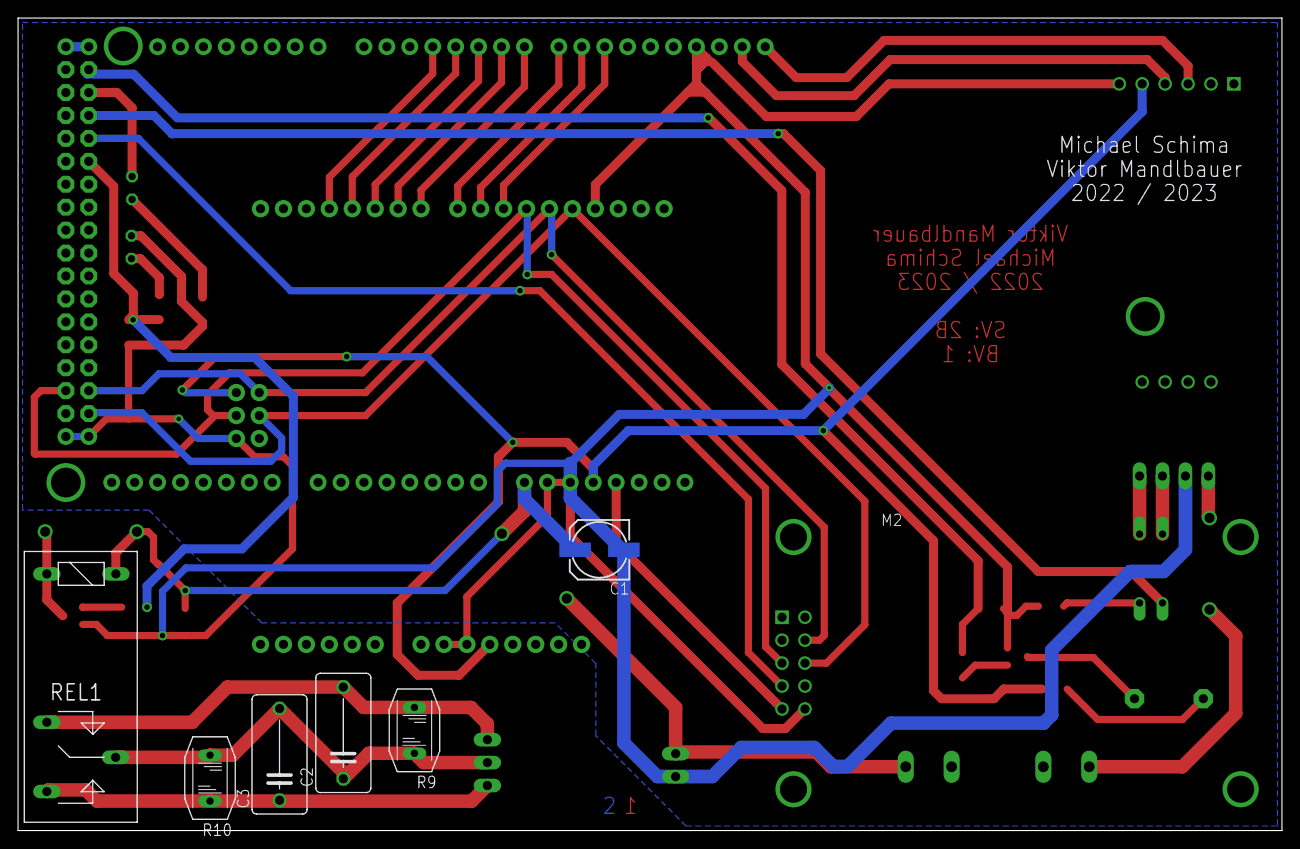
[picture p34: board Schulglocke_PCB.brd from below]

Board: 2 copper layers, 140.0 x 90.0 mm, 35 parts (7 on the bottom side), 38 nets.

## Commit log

2022-10-02 erster schaltplan mit allen esenziellen bauteilen
    [firstattempt.kicad_pcb, firstattempt.kicad_sch]
2023-01-22 neuer schaltplan jetzt in eagle
    [Schulglocke_PCB.sch, firstattempt.kicad_pcb, firstattempt.kicad_sch]
2023-01-22 demo gehäuse
    [demo1-Body.3mf, demo1.FCStd, demo1_cut.FCStd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]
2023-01-22 correct folder name
    [Schulglocke_PCB.sch]
2023-01-22 korrektur ueberhang
    [demo1_cut-Body006.3mf, demo1_cut.FCStd]
2023-02-19 korekte bauteile
    [Schulglocke_PCB.sch]
2023-02-19 neue numerierung
    [Schulglocke_PCB.sch]
2023-03-09 before change
    [Schulglocke_PCB.brd, Schulglocke_PCB.sch]
2023-03-09 leiterplatte plaziert
    [Schulglocke_PCB.brd, Schulglocke_PCB.sch]
2023-03-13 mit traces noch ohne montagelöcher und ohne anpassung footprints
    [Schulglocke_PCB.brd, Schulglocke_PCB.sch]
2023-03-16 added drill holes
    [Schulglocke_PCB.brd, Schulglocke_PCB.sch]
2023-03-23 changed ds clock layou
    [Schulglocke_PCB.brd, Schulglocke_PCB.dxf, Schulglocke_PCB.sch]
2023-03-26 final version
    [Schulglocke_PCB.brd, Schulglocke_PCB.dxf, Schulglocke_PCB.sch]
2023-03-26 flipped buzzer
    [Schulglocke_PCB.brd, Schulglocke_PCB.dxf, Schulglocke_PCB.sch]
2023-04-30 korrigiere lan abd
    [1-Body007.3mf, 1-base body witch cut out001.3mf, 1.3mf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]
2023-04-30 clean freecad prj
    [1.FCStd]
2023-04-30 2 case versions
    [1.FCStd, 1_long edge.FCStd]
2023-05-30 fixed a name
    [Schulglocke_PCB.brd, Schulglocke_PCB.sch]
2023-05-30 freecad cad files
    [1-base body witch cut out001.3mf, 1.FCStd, isolation-Body.3mf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]
